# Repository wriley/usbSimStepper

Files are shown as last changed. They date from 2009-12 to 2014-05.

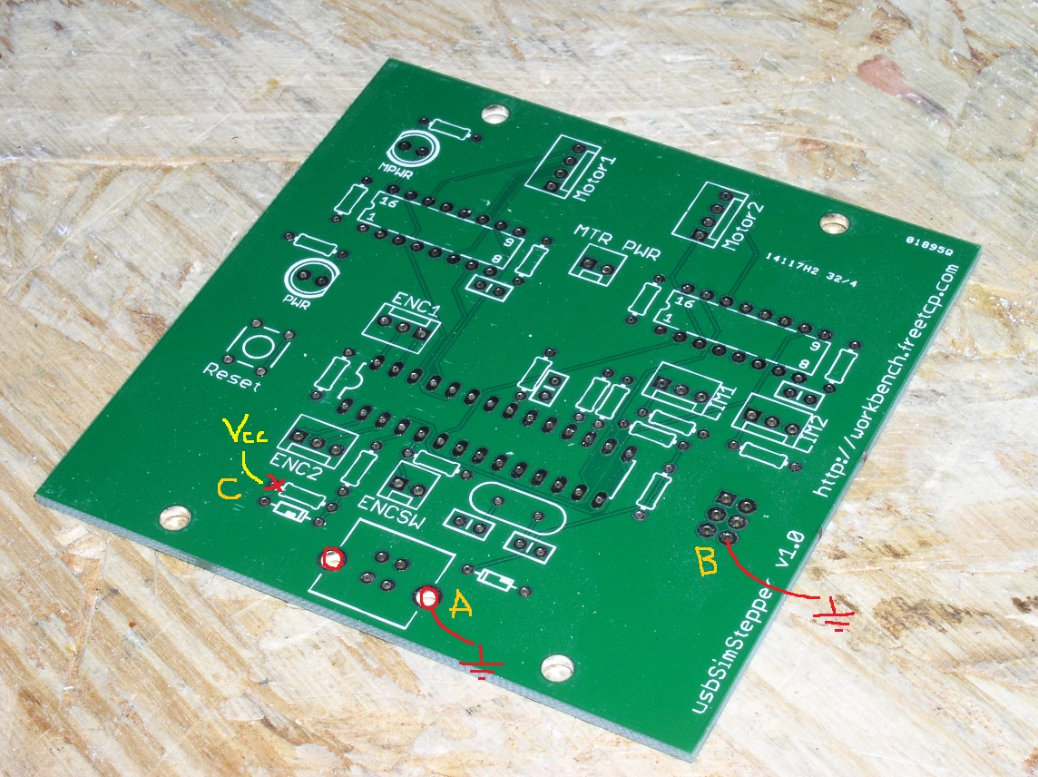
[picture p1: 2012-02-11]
pcb/usbSimStepper v1.0 pcb repair 1.jpg

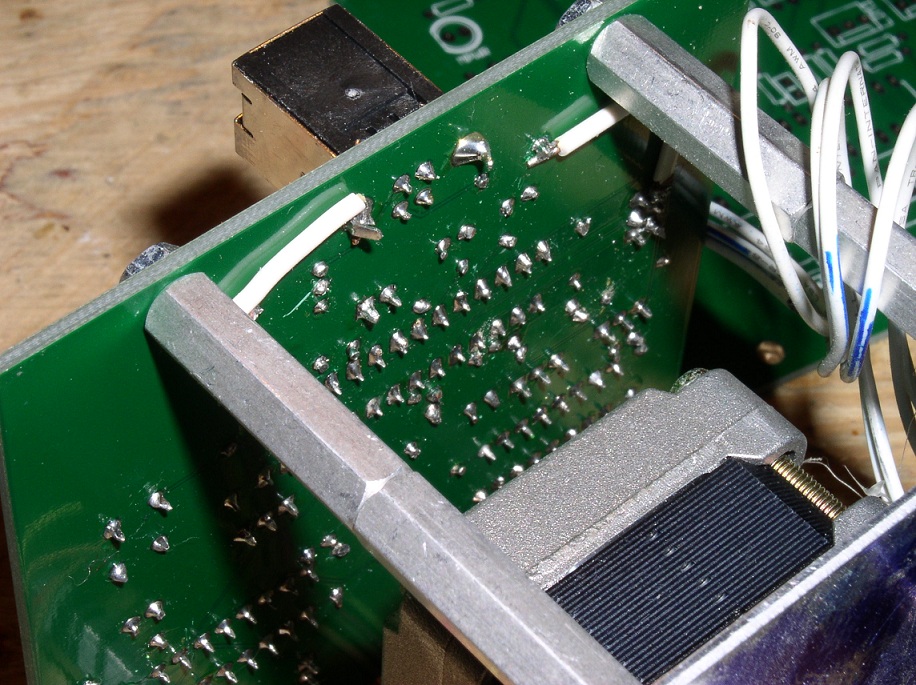
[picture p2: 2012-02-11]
pcb/usbSimStepper v1.0 pcb repair 3.jpg

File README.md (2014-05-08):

usbSimStepper
=============

This is a half-finished project I started several years ago for a flight simulator panel. It is a USB driver board for 1-2 stepper motors built for instruments from Mike Powell's book Building Simulated Aircraft Instrumentation<sup>1</sup>. Windows programs, such as usbSimCentral<sup>2</sup>, can interface with this board via a DLL<sup>3</sup>.

Relevant blog posts
* http://workbench.freetcp.com/archives/549
* http://workbench.freetcp.com/archives/555
* http://workbench.freetcp.com/archives/571
* http://workbench.freetcp.com/archives/739
* http://workbench.freetcp.com/archives/745

References

1. http://www.mikesflightdeck.com/mfdb/bsai/bsai.html
2. https://github.com/wriley/usbSimCentral
3. https://github.com/wriley/usbSimInstrument

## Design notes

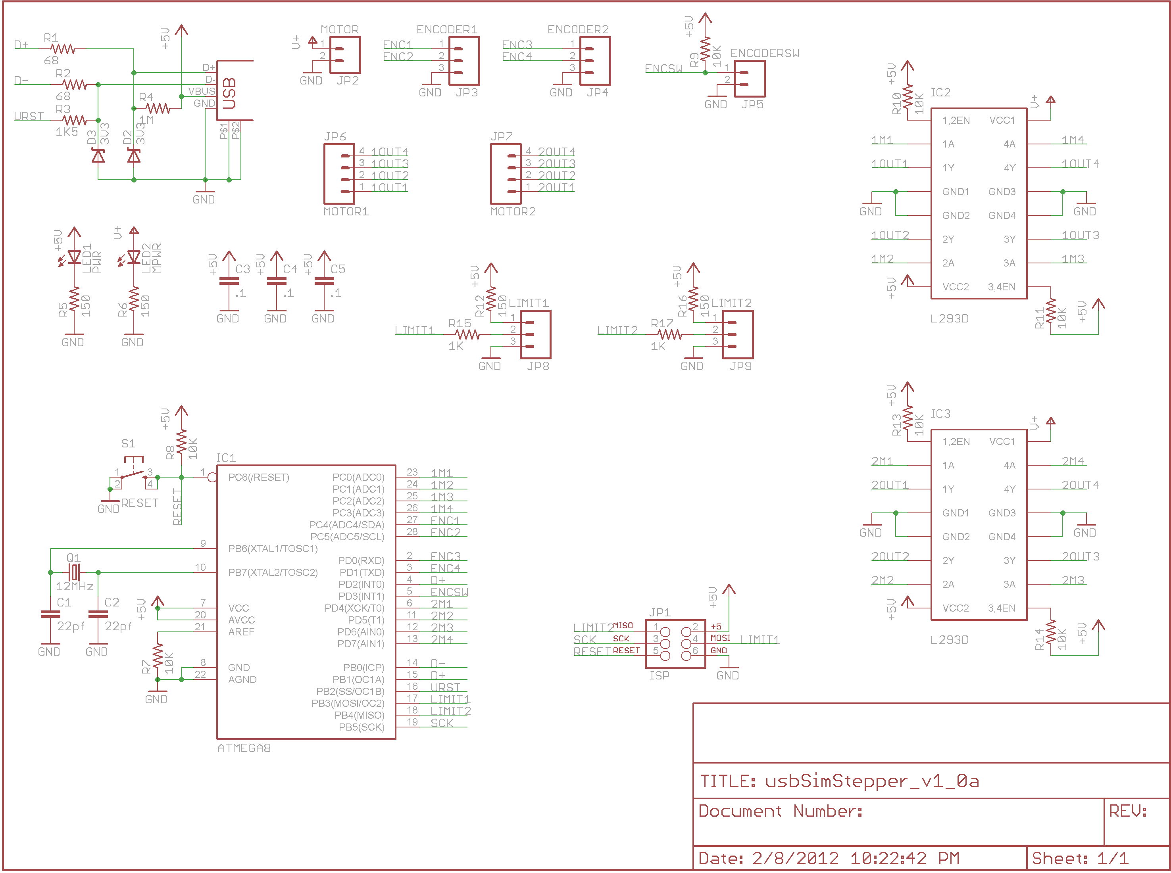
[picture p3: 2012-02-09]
pcb/usbSimStepper_v1_0a_schematic.png

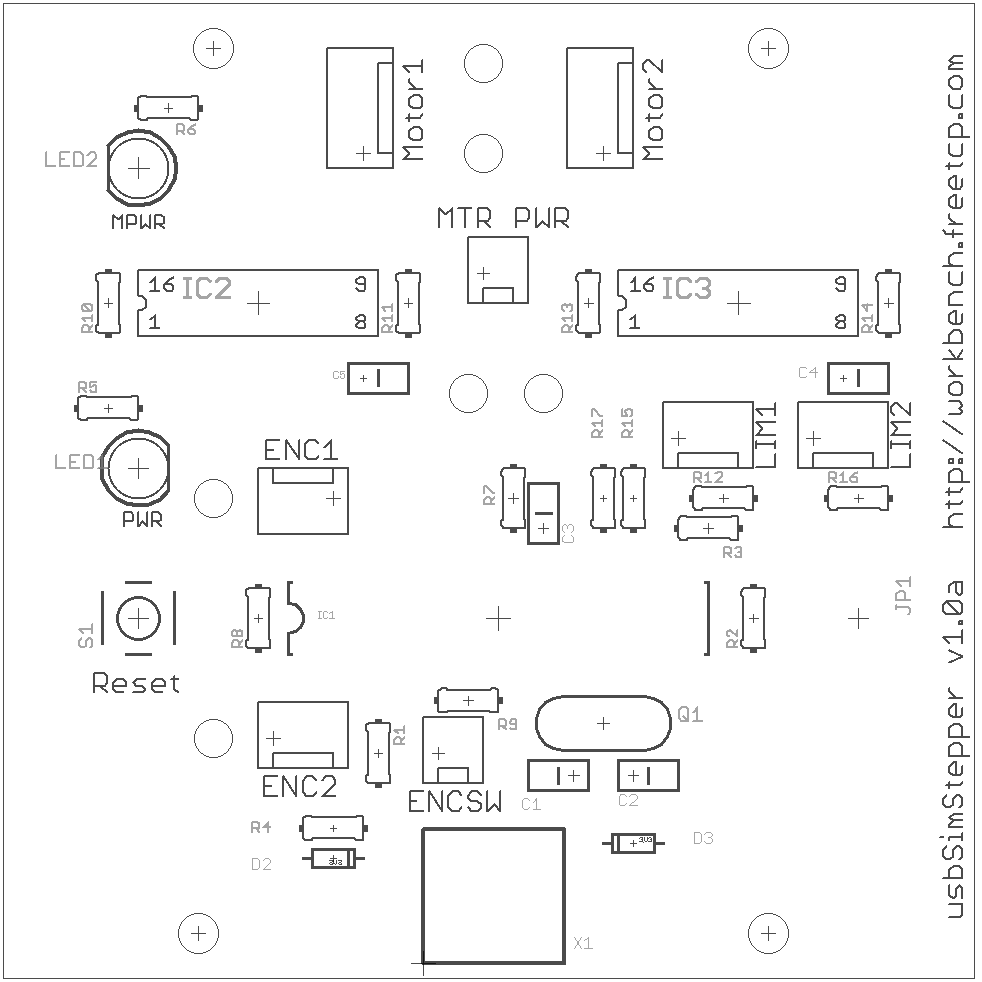
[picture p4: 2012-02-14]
pcb/usbSimStepper_v1_0a_silkscreen.png

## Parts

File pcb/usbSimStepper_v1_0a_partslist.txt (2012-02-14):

Partlist

Exported from usbSimStepper_v1_0a.brd at 2/13/2012 9:21:40 PM

EAGLE Version 6.1.0 Copyright (c) 1988-2012 CadSoft

Assembly variant: 

Part     Value          Package            Library  Position (inch)       Orientation

C1       22pf           CAP-PTH-SMALL2     SparkFun (1.9 0.675)           R180
C2       22pf           CAP-PTH-SMALL2     SparkFun (2.1 0.675)           R0
C3       .1             CAP-PTH-SMALL2     SparkFun (1.8 1.5)             R90
C4       .1             CAP-PTH-SMALL2     SparkFun (2.8 2)               R0
C5       .1             CAP-PTH-SMALL2     SparkFun (1.2 2)               R0
D2       3V3            DIODE-ZENER        SparkFun (1.1 0.4)             R180
D3       3V3            DIODE-ZENER        SparkFun (2.1 0.45)            R0
IC1      ATMEGA8        DIL28-3            SparkFun (1.65 1.2)            R0
IC2      L293D          DIL16              sgs-thom (0.85 2.25)           R0
IC3      L293D          DIL16              sgs-thom (2.45 2.25)           R0
JP1      ISP            2X3-NS             SparkFun (2.85 1.2)            R270
JP2      MOTOR          MOLEX-1X2          SparkFun (1.6 2.35)            R0
JP3      ENCODER1       MOLEX-1X3          SparkFun (1.1 1.6)             R180
JP4      ENCODER2       MOLEX-1X3          SparkFun (0.9 0.8)             R0
JP5      ENCODERSW      MOLEX-1X2          SparkFun (1.45 0.75)           R0
JP6      MOTOR1         MOLEX-1X4          SparkFun (1.2 2.75)            R90
JP7      MOTOR2         MOLEX-1X4          SparkFun (2 2.75)              R90
JP8      LIMIT1         MOLEX-1X3          SparkFun (2.25 1.8)            R0
JP9      LIMIT2         MOLEX-1X3          SparkFun (2.7 1.8)             R0
LED1     PWR            LED5MM             SparkFun (0.45 1.7)            R0
LED2     MPWR           LED5MM             SparkFun (0.45 2.7)            R180
Q1       12MHz          HC49US             SparkFun (2 0.85)              R0
R1       68             0204/7             resistor (1.25 0.75)           R270
R2       68             0204/7             resistor (2.5 1.2)             R90
R3       1K5            0204/7             resistor (2.35 1.5)            R0
R4       1M             0204/7             resistor (1.1 0.5)             R180
R5       150            0204/7             resistor (0.35 1.9)            R0
R6       150            0204/7             resistor (0.55 2.9)            R180
R7       10K            0204/7             resistor (1.7 1.6)             R270
R8       10K            0204/7             resistor (0.85 1.2)            R90
R9       10K            0204/7             resistor (1.55 0.925)          R0
R10      10K            0204/7             resistor (0.35 2.25)           R90
R11      10K            0204/7             resistor (1.35 2.25)           R90
R12      150            0204/7             resistor (2.4 1.6)             R0
R13      10K            0204/7             resistor (1.95 2.25)           R90
R14      10K            0204/7             resistor (2.95 2.25)           R90
R15      1K             0204/7             resistor (2.1 1.6)             R90
R16      150            0204/7             resistor (2.85 1.6)            R0
R17      1K             0204/7             resistor (2 1.6)               R90
S1       RESET          TACTILE-PTH        SparkFun (0.45 1.2)            R90
X1       USB            USB-B-PTH-VERTICAL SparkFun (1.4 0.05)            R0

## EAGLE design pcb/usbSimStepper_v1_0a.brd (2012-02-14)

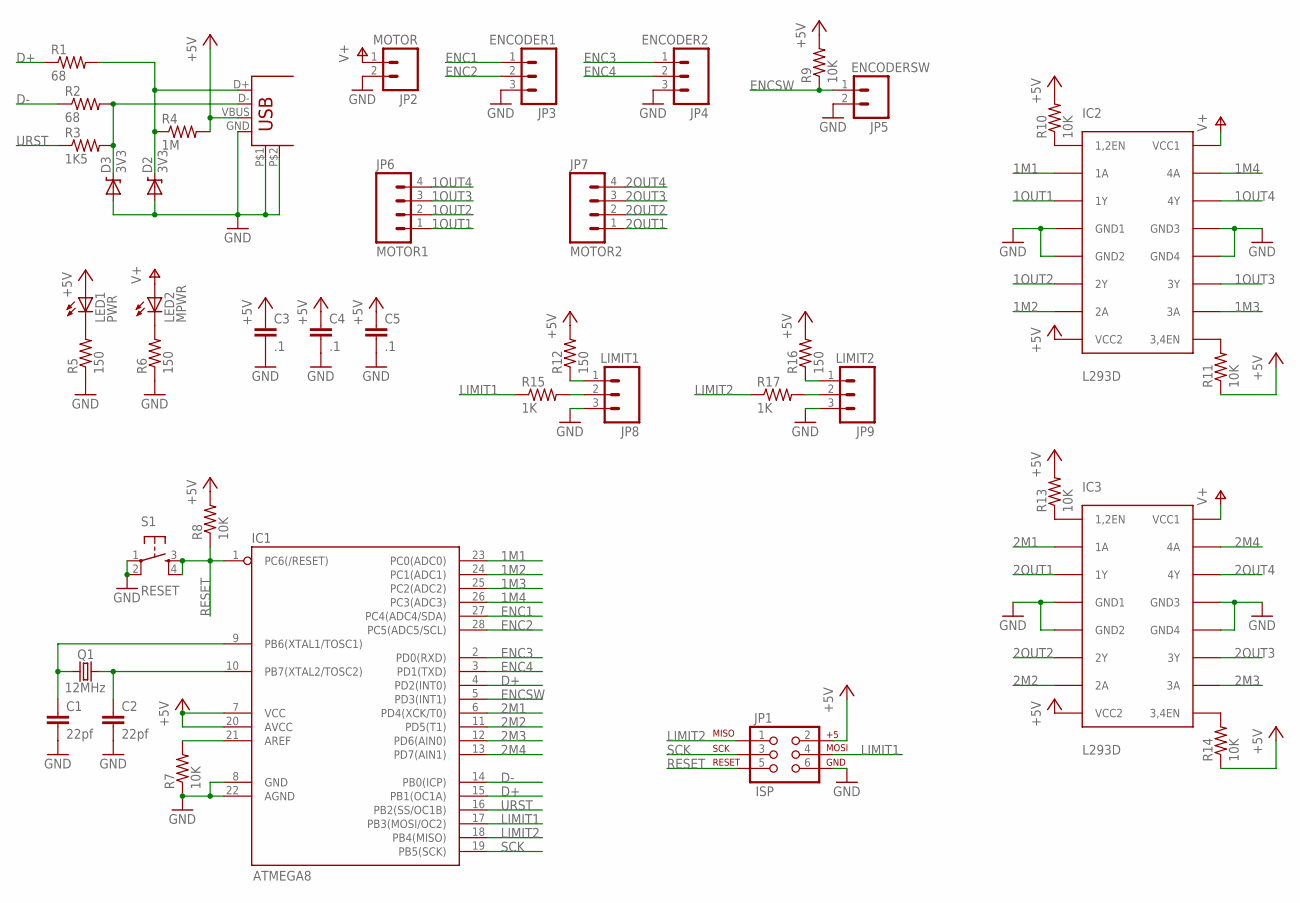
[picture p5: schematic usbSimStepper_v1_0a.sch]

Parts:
C1, C2: 22pf; CAP-PTH-SMALL2
C3, C4, C5: .1; CAP-PTH-SMALL2
D2, D3: 3V3; DIODE-ZENER
IC1: ATMEGA8; DIL28-3
IC2, IC3: L293D; DIL16
JP1: ISP; 2X3-NS
JP2: MOTOR; MOLEX-1X2
JP3: ENCODER1; MOLEX-1X3
JP4: ENCODER2; MOLEX-1X3
JP5: ENCODERSW; MOLEX-1X2
JP6: MOTOR1; MOLEX-1X4
JP7: MOTOR2; MOLEX-1X4
JP8: LIMIT1; MOLEX-1X3
JP9: LIMIT2; MOLEX-1X3
LED1: PWR; LED5MM
LED2: MPWR; LED5MM
Q1: 12MHz; HC49US
R1, R2: 68; 0204/7
R3: 1K5; 0204/7
R4: 1M; 0204/7
R5, R6, R12, R16: 150; 0204/7
R7, R8, R9, R10, R11, R13, R14: 10K; 0204/7
R15, R17: 1K; 0204/7
S1: RESET; TACTILE-PTH
X1: USB; USB-B-PTH-VERTICAL

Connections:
1M1: IC1.23 (PC0(ADC0)), IC2.2 (1A)
1M2: IC1.24 (PC1(ADC1)), IC2.7 (2A)
1M3: IC1.25 (PC2(ADC2)), IC2.10 (3A)
1M4: IC1.26 (PC3(ADC3)), IC2.15 (4A)
1OUT1: IC2.3 (1Y), JP6.1
1OUT2: IC2.6 (2Y), JP6.2
1OUT3: IC2.11 (3Y), JP6.3
1OUT4: IC2.14 (4Y), JP6.4
2M1: IC1.6 (PD4(XCK/T0)), IC3.2 (1A)
2M2: IC1.11 (PD5(T1)), IC3.7 (2A)
2M3: IC1.12 (PD6(AIN0)), IC3.10 (3A)
2M4: IC1.13 (PD7(AIN1)), IC3.15 (4A)
2OUT1: IC3.3 (1Y), JP7.1
2OUT2: IC3.6 (2Y), JP7.2
2OUT3: IC3.11 (3Y), JP7.3
2OUT4: IC3.14 (4Y), JP7.4
+5V: C3.1, C4.1, C5.1, IC1.7 (VCC), IC1.20 (AVCC), IC2.8 (VCC2), IC3.8 (VCC2), JP1.2, LED1.A, R4.2, R8.2, R9.2, R10.2, R11.1, R12.2, R13.2, R14.1, R16.2, X1.VBUS
D+: IC1.4 (PD2(INT0)), IC1.15 (PB1(OC1A)), R1.1
D-: IC1.14 (PB0(ICP)), R2.1
ENC1: IC1.27 (PC4(ADC4/SDA)), JP3.1
ENC2: IC1.28 (PC5(ADC5/SCL)), JP3.2
ENC3: IC1.2 (PD0(RXD)), JP4.1
ENC4: IC1.3 (PD1(TXD)), JP4.2
ENCSW: IC1.5 (PD3(INT1)), JP5.1, R9.1
GND: C1.2, C2.2, C3.2, C4.2, C5.2, D2.P$2 (A), D3.P$2 (A), IC1.8 (GND), IC1.22 (AGND), IC2.4 (GND1), IC2.5 (GND2), IC2.12 (GND4), IC2.13 (GND3), IC3.4 (GND1), IC3.5 (GND2), IC3.12 (GND4), IC3.13 (GND3), JP1.6, JP2.2, JP3.3, JP4.3, JP5.2, JP8.3, JP9.3, R5.1, R6.1, R7.1, S1.1, S1.2, X1.GND, X1.P$1, X1.P$2
LIMIT1: IC1.17 (PB3(MOSI/OC2)), JP1.4, R15.1
LIMIT2: IC1.18 (PB4(MISO)), JP1.1, R17.1
unnamed: D3.P$1 (C), R2.2, R3.2, X1.D-
unnamed: D2.P$1 (C), R1.2, R4.1, X1.D+
unnamed: LED1.K (C), R5.2
unnamed: LED2.K (C), R6.2
unnamed: C1.1, IC1.9 (PB6(XTAL1/TOSC1)), Q1.1
unnamed: C2.1, IC1.10 (PB7(XTAL2/TOSC2)), Q1.2
unnamed: IC1.21 (AREF), R7.2
unnamed: JP8.1, R12.1
unnamed: JP8.2, R15.2
unnamed: JP9.1, R16.1
unnamed: IC3.1 (1,2EN), R13.1
unnamed: IC3.9 (3,4EN), R14.2
unnamed: IC2.1 (1,2EN), R10.1
unnamed: IC2.9 (3,4EN), R11.2
unnamed: JP9.2, R17.2
RESET: IC1.1 (PC6(/RESET)), JP1.5, R8.1, S1.3, S1.4
SCK: IC1.19 (PB5(SCK)), JP1.3
URST: IC1.16 (PB2(SS/OC1B)), R3.1
V+: IC2.16 (VCC1), IC3.16 (VCC1), JP2.1, LED2.A

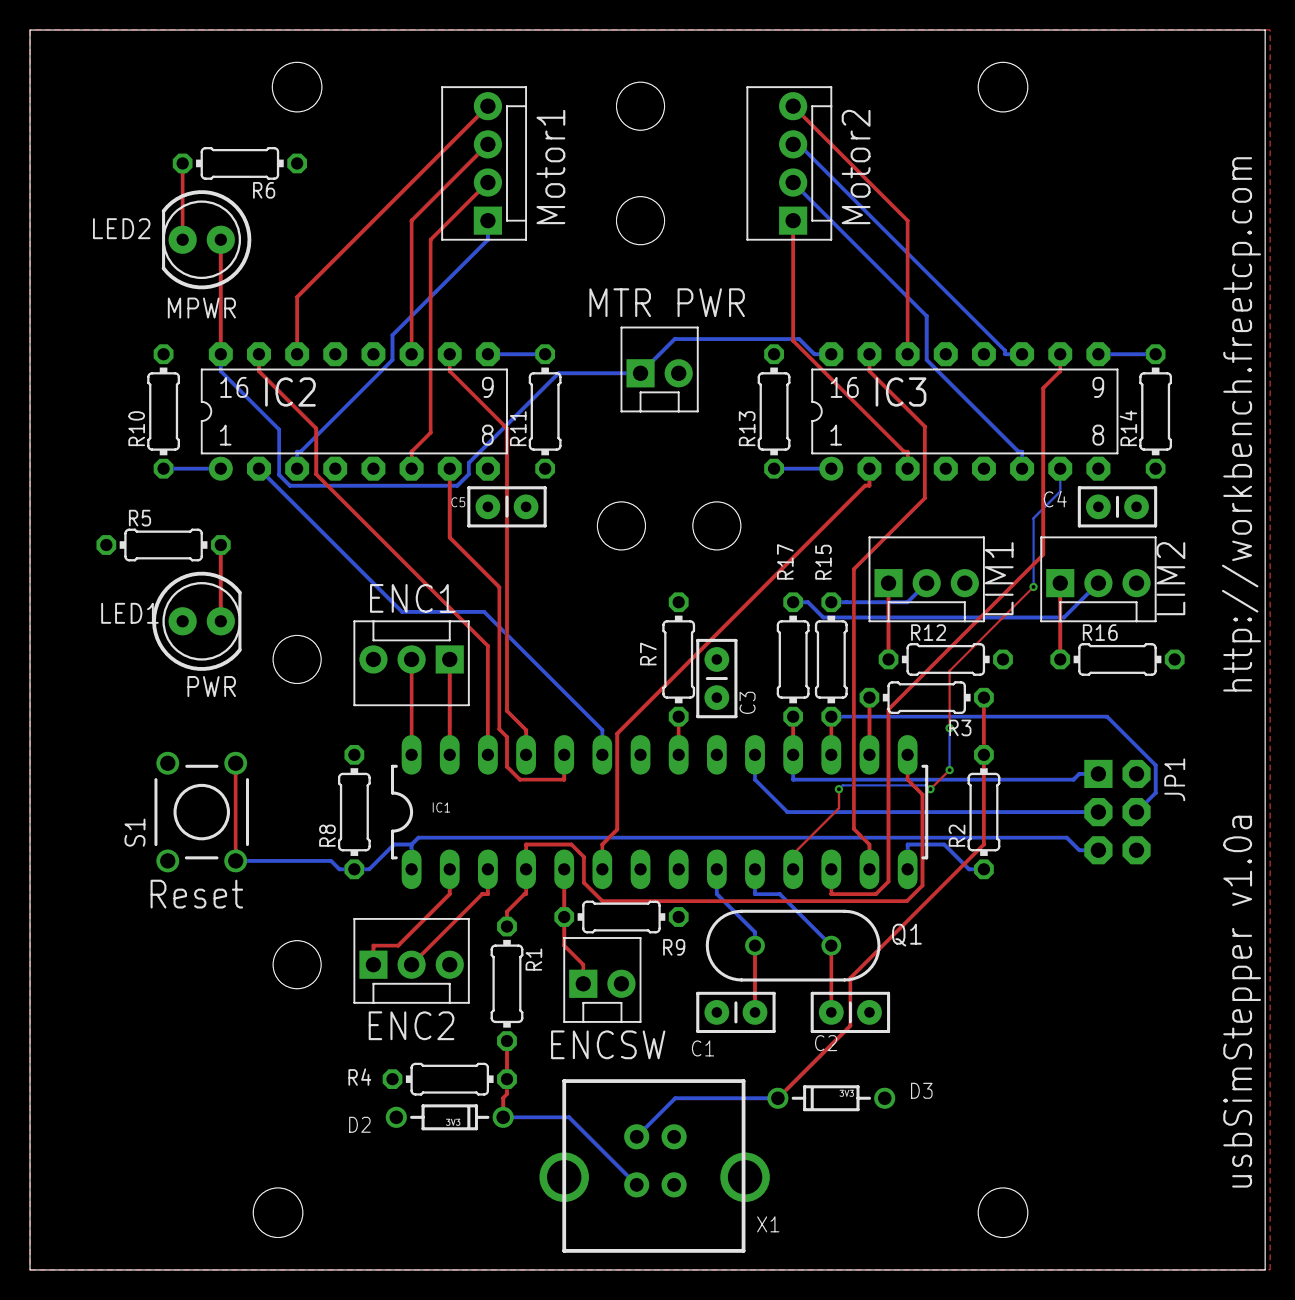
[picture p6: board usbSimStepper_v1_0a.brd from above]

Board: 2 copper layers, 82.2 x 82.5 mm, 45 parts (0 on the bottom side), 46 nets.

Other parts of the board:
U$1, U$2, U$3, U$4: STAND-OFF

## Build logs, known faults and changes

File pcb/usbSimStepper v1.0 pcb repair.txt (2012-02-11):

usbSimStepper v1.0 PCB error repair notes

Reference image "usbSimStepper v1.0 pcb repair 1.jpg" for steps A, B, and C.
A) The USB connector shields are not tied to GND (bottom plane).
   Connect either shield connection to any convenient GND location

B) The GND pin on the ISP connector (2x3-pin header) is not tied to GND (bottom plane).
   Connect pin 6 to any convenient GND location

C) Resistor R4 is tied to GND (bottom plane) instead of Vcc (top plane).
   Do not solder the end of R4 marked with red X, instead connect that end to any
   convenient Vcc location.

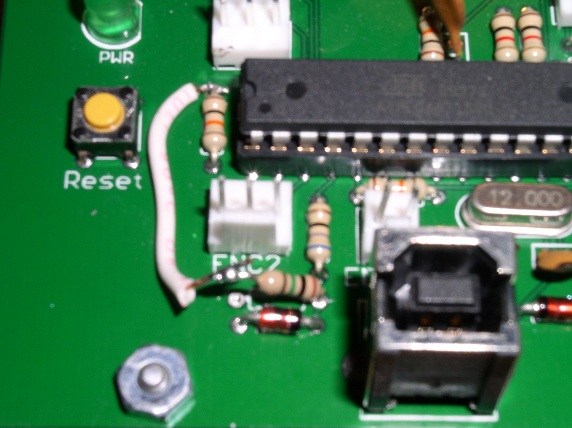
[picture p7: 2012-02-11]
pcb/usbSimStepper v1.0 pcb repair 2.jpg

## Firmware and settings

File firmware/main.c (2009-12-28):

#include <stdlib.h>
#include <avr/io.h>
#include <avr/interrupt.h>
#include <avr/pgmspace.h>
#include <avr/eeprom.h>
#include <avr/wdt.h>

#include "usbdrv.h"
#include "oddebug.h"
#include <util/delay.h>

// Uncomment if instrument is meant to go in continuous circles, such as a gyrocompass
// Comment out for instruments such as ASI
//#define FULLCIRCLE

// Uncomment to support second stepper motor, opto and encoder
//#define MOTOR2

#define ENCODER1PORT            PORTD
#define ENCODER1DDR             DDRD
#define ENCODER1PIN             PIND
#define PHASE_A_1               (ENCODER1PIN & 1<<1)
#define PHASE_B_1               (ENCODER1PIN & 1<<0)
#define OPTO1PORT               PORTB
#define OPTO1DDR                DDRB
#define OPTO1PIN                PINB
#define OPTO1                   (OPTO1PIN & 1<<3)
#define MOTOR1PORT              PORTC
#define MOTOR1DDR               DDRC
#define MOTOR1MASK				0x0f

#define CMD_ECHO				0
#define CMD_SET1				1
#define CMD_SET2				2
#define CMD_GET_TABLE			10
#define CMD_SET_TABLE			11
#define CMD_GET_TABLERAW		20
#define CMD_SET_TABLERAW		21
#ifdef MOTOR2
#define CMD_GET_TABLE2			30
#define CMD_SET_TABLE2			31
#define CMD_GET_TABLERAW2		40
#define CMD_SET_TABLERAW2		41
#endif
#define CMD_RESET				99

#ifdef MOTOR2
#define ENCODER2PORT            PORTD
#define ENCODER2DDR             DDRD
#define ENCODER2PIN             PIND
#define PHASE_A_2               (ENCODER2PIN & 1<<1)
#define PHASE_B_2               (ENCODER2PIN & 1<<0)
#define OPTO2PORT               PORTB
#define OPTO2DDR                DDRB
#define OPTO2PIN                PINB
#define OPTO2                   (OPTO2PIN & 1<<3)
#define MOTOR2PORT              PORTC
#define MOTOR2DDR               DDRC
#define MOTOR2MASK				0x0f
#endif

#define FORWARD                 0
#define REVERSE                 1
#define HALFWAY					199
#define MAXPOS					399
#define EEPROM_SERIAL_LOCATION	0

#define EEPROM_TABLE_LOCATION		8
#define EEPROM_TABLERAW_LOCATION	72
#ifdef MOTOR2
#define EEPROM_TABLE2_LOCATION		136
#define EEPROM_TABLERAW2_LOCATION	200
#endif

// positions for half stepping bipolar
static char motorPositions[8] = {
    0x09,   // 0 0 0 0  1 0 0 1
    0x01,   // 0 0 0 0  0 0 0 1
    0x05,   // 0 0 0 0  0 1 0 1
    0x04,   // 0 0 0 0  0 1 0 0
    0x06,   // 0 0 0 0  0 1 1 0
    0x02,   // 0 0 0 0  0 0 1 0
    0x0a,   // 0 0 0 0  1 0 1 0
    0x08    // 0 0 0 0  1 0 0 0
};

static int16_t last1;
static int16_t position1 = 0;
static int16_t newposition1 = 0;
static int8_t mtr_direction1 = REVERSE;
static int16_t stepCounter1 = 0;
static int16_t mtr_delta1 = 0x0000;
static int8_t goHome1 = 0x02;
static int16_t testCount1 = 0;

#ifdef MOTOR2
static int16_t last2;
static int16_t position2 = 0;
static int16_t newposition2 = 0;
static int8_t mtr_direction2 = REVERSE;
static int16_t stepCounter2 = 0;
static int16_t mtr_delta2 = 0x0000;
static int8_t goHome2 = 0x02;
static int16_t testCount2 = 0;
#endif

#define SERIAL_NUMBER_LENGTH 1
static int  serialNumberDescriptor[SERIAL_NUMBER_LENGTH + 1];

static void SetSerial(void)
{
   serialNumberDescriptor[0] = USB_STRING_DESCRIPTOR_HEADER(SERIAL_NUMBER_LENGTH);
   serialNumberDescriptor[1] = eeprom_read_byte(EEPROM_SERIAL_LOCATION);
}

USB_PUBLIC uchar usbFunctionSetup(uchar data[8])
{
usbRequest_t    *rq = (void *)data;
static uchar    replyBuf[8];

    usbMsgPtr = replyBuf;
    if(rq->bRequest == CMD_ECHO){
        replyBuf[0] = rq->wValue.bytes[0];
        replyBuf[1] = rq->wValue.bytes[1];
        return 2;
    } else if(rq->bRequest == CMD_SET1){
		newposition1 = 0x0000;
		newposition1 <<= 8;
        newposition1 |= rq->wValue.bytes[1];
		newposition1 <<= 8;
        newposition1 |= rq->wValue.bytes[0];
#ifdef MOTOR2
	} else if(rq->bRequest == CMD_SET2){
		newposition2 = 0x0000;
		newposition2 <<= 8;
        newposition2 |= rq->wValue.bytes[1];
		newposition2 <<= 8;
        newposition2 |= rq->wValue.bytes[0];
#endif
    } else if(rq->bRequest == CMD_GET_TABLE){
		for(uchar i = 0; i < 8; i++){
			replyBuf[i] = eeprom_read_byte(EEPROM_TABLE_LOCATION + (rq->wValue.bytes[0] * 8) + i);
		}
		return 8;
    } else if(rq->bRequest == CMD_SET_TABLE){
		eeprom_write_byte(EEPROM_TABLE_LOCATION + (rq->wValue.bytes[0] * 8) + (rq->wValue.bytes[1]), rq->wIndex.bytes[0]);
	} else if(rq->bRequest == CMD_GET_TABLERAW){
		for(uchar i = 0; i < 8; i++){
			replyBuf[i] = eeprom_read_byte(EEPROM_TABLERAW_LOCATION + (rq->wValue.bytes[0] * 8) + i);
		}
		return 8;
    } else if(rq->bRequest == CMD_SET_TABLERAW){
		eeprom_write_byte(EEPROM_TABLERAW_LOCATION + (rq->wValue.bytes[0] * 8) + (rq->wValue.bytes[1]), rq->wIndex.bytes[0]);
#ifdef MOTOR2
    } else if(rq->bRequest == CMD_GET_TABLE2){
		for(uchar i = 0; i < 8; i++){
			replyBuf[i] = eeprom_read_byte(EEPROM_TABLE2_LOCATION + (rq->wValue.bytes[0] * 8) + i);
		}
		return 8;
    } else if(rq->bRequest == CMD_SET_TABLE2){
		eeprom_write_byte(EEPROM_TABLE2_LOCATION + (rq->wValue.bytes[0] * 8) + (rq->wValue.bytes[1]), rq->wIndex.bytes[0]);
	} else if(rq->bRequest == CMD_GET_TABLERAW2){
		for(uchar i = 0; i < 8; i++){
			replyBuf[i] = eeprom_read_byte(EEPROM_TABLERAW2_LOCATION + (rq->wValue.bytes[0] * 8) + i);
		}
		return 8;
    } else if(rq->bRequest == CMD_SET_TABLERAW2){
		eeprom_write_byte(EEPROM_TABLERAW2_LOCATION + (rq->wValue.bytes[0] * 8) + (rq->wValue.bytes[1]), rq->wIndex.bytes[0]);
#endif
	} else if(rq->bRequest == CMD_RESET){
		newposition1 = 0;
		position1 = 0;
		goHome1 = 2;
    }
    return 0;
}

uchar usbFunctionDescriptor(usbRequest_t *rq)
{
   uchar len = 0;
   usbMsgPtr = 0;
   if (rq->wValue.bytes[1] == USBDESCR_STRING && rq->wValue.bytes[0] == 3)
   {
      usbMsgPtr = (uchar*)serialNumberDescriptor;
      len = sizeof(serialNumberDescriptor);
   }
   return len;
}

SIGNAL (SIG_OUTPUT_COMPARE2)                // 1ms
{
    int16_t new1, diff1;

    new1 = 0;
    if( PHASE_A_1 )
        new1 = 3;
    if( PHASE_B_1 )
        new1 ^= 1;                          // convert gray to binary
    diff1 = last1 - new1;                   // difference last - new
    if( diff1 & 1 ){                        // bit 0 = value (1)
        last1 = new1;                       // store new as next last
		position1 += (diff1 & 2) - 1;		// update position1
    }

#ifdef MOTOR2
	int16_t new2, diff2;

    new2 = 0;
    if( PHASE_A_2 )
        new2 = 3;
    if( PHASE_B_2 )
        new2 ^= 1;                          // convert gray to binary
    diff2 = last2 - new2;                   // difference last - new
    if( diff2 & 1 ){                        // bit 0 = value (1)
        last2 = new2;                       // store new as next last
		position2 += (diff2 & 2) - 1;		// update position1
    }
#endif

    if(goHome1 > 0)
    {
		if(goHome1 == 3) // test mode
		{
			if(testCount1 < MAXPOS)
			{
				testCount1++;
				stepCounter1++;
				stepCounter1 &= 0x07;
            	MOTOR1PORT = motorPositions[stepCounter1] & MOTOR1MASK;
			}
			else
			{
				goHome1 = 4;
			}
		}

        if(goHome1 == 2) // move forward until opto is not dark
        {
            if(OPTO1PIN & OPTO1) // dark
            {
                stepCounter1++;
				stepCounter1 &= 0x07;
                MOTOR1PORT = motorPositions[stepCounter1] & MOTOR1MASK;
            }
            else
            {
                goHome1 = 1;
            }
        }
        
        if(goHome1 == 1) // move backward until opto is dark
        {
            if(OPTO1PIN & OPTO1) // dark
            {
                goHome1 = 0;
            }
            else
            {
                stepCounter1--;
				stepCounter1 &= 0x07;
                MOTOR1PORT = motorPositions[stepCounter1] & MOTOR1MASK;
            }
        }
    }
    else
    {
		if(newposition1 > MAXPOS) { newposition1 = MAXPOS; }
		if(newposition1 < 0) { newposition1 = 0; }
        mtr_delta1 = newposition1 - position1;
        if(mtr_delta1 != 0)
        {
            if(mtr_delta1 < 0)
            {
                mtr_direction1 = REVERSE;
            }
            else
            {
                mtr_direction1 = FORWARD;
            }

#ifdef FULLCIRCLE
            if(abs(mtr_delta1) > HALFWAY)
            {
                if(mtr_direction1 == FORWARD)
                {
                    mtr_direction1 = REVERSE;
                } else if(mtr_direction1 == REVERSE)
				{
					mtr_direction1 = FORWARD;
				}
            }
#endif

            if(mtr_direction1 == REVERSE)
            {
                position1--;
#ifdef FULLCIRCLE
				if(position1 < 0){ position1 = MAXPOS; }
#else
				if(position1 < 0){ position1 = 0; }
#endif
                stepCounter1--;
            }
            else
            {
                position1++;
#ifdef FULLCIRCLE
                if(position1 > MAXPOS){ position1 = 0; }
#else
				if(position1 > MAXPOS){ position1 = MAXPOS; }
#endif
				stepCounter1++;
            }
            
			stepCounter1 &= 0x07;
            MOTOR1PORT = motorPositions[stepCounter1] & MOTOR1MASK;
        }
    }

#ifdef MOTOR2
    if(goHome2 > 0)
    {
		if(goHome2 == 3) // test mode
		{
			if(testCount2 < MAXPOS)
			{
				testCount2++;
				stepCounter2++;
				stepCounter2 &= 0x07;
            	MOTOR2PORT = motorPositions[stepCounter2] & MOTOR2MASK;
			}
			else
			{
				goHome2 = 4;
			}
		}

        if(goHome2 == 2) // move forward until opto is not dark
        {
            if(OPTO2PIN & OPTO2) // dark
            {
                stepCounter2++;
				stepCounter2 &= 0x07;
                MOTOR2PORT = motorPositions[stepCounter2] & MOTOR2MASK;
            }
            else
            {
                goHome2 = 1;
            }
        }
        
        if(goHome2 == 1) // move backward until opto is dark
        {
            if(OPTO2PIN & OPTO2) // dark
            {
                goHome2 = 0;
            }
            else
            {
                stepCounter2--;
				stepCounter2 &= 0x07;
                MOTOR2PORT = motorPositions[stepCounter2] & MOTOR2MASK;
            }
        }
    }
    else
    {
		if(newposition2 > MAXPOS) { newposition2 = MAXPOS; }
		if(newposition2 < 0) { newposition2 = 0; }
        mtr_delta2 = newposition2 - position2;
        if(mtr_delta2 != 0)
        {
            if(mtr_delta2 < 0)
            {
                mtr_direction2 = REVERSE;
            }
            else
            {
                mtr_direction2 = FORWARD;
            }

#ifdef FULLCIRCLE
            if(abs(mtr_delta2) > HALFWAY)
            {
                if(mtr_direction2 == FORWARD)
                {
                    mtr_direction2 = REVERSE;
                } else if(mtr_direction2 == REVERSE)
				{
					mtr_direction2 = FORWARD;
				}
            }
#endif

            if(mtr_direction2 == REVERSE)
            {
                position2--;
#ifdef FULLCIRCLE
				if(position2 < 0){ position2 = MAXPOS; }
#else
				if(position2 < 0){ position2 = 0; }
#endif
                stepCounter2--;
            }
            else
            {
                position2++;
#ifdef FULLCIRCLE
                if(position2 > MAXPOS){ position2 = 0; }
#else
				if(position2 > MAXPOS){ position2 = MAXPOS; }
#endif
				stepCounter2++;
            }
            
			stepCounter2 &= 0x07;
            MOTOR2PORT = motorPositions[stepCounter2] & MOTOR2MASK;
        }
    }
#endif
}

int main(void)
{
	uchar   i;

	SetSerial();

    wdt_enable(WDTO_1S);
    odDebugInit();
    DDRD = ~(1 << 2);   /* all outputs except PD2 = INT0 */
    PORTD = 0;
    PORTB = 0;          /* no pullups on USB pins */
/* We fake an USB disconnect by pulling D+ and D- to 0 during reset. This is
 * necessary if we had a watchdog reset or brownout reset to notify the host
 * that it should re-enumerate the device. Otherwise the host's and device's
 * concept of the device-ID would be out of sync.
 */
    DDRB = ~USBMASK;    /* set all pins as outputs except USB */
    usbDeviceDisconnect();  /* enforce re-enumeration, do this while interrupts are disabled! */
    i = 0;
    while(--i){         /* fake USB disconnect for > 500 ms */
        wdt_reset();
        _delay_ms(2);
    }
    usbDeviceConnect();
    TCCR0 = 5;          /* set prescaler to 1/1024 */
    usbInit();

	DDRB &= ~(_BV(PB3));
	PORTB |= _BV(PB3);
	
	DDRD &= ~(_BV(PD0)|_BV(PD1));
	PORTD |= (_BV(PD0)|_BV(PD1));

	TCNT2 = 0x00; /* Timer 2: Reset counter (periodic timer) */
	TCCR2 = 0x0f; /* Clock / 1024, clear after compare match (CTC) */
	OCR2 = 0x0b;

	TIMSK |= _BV(OCIE2);

	DDRC = 0x2f;
	PORTC = 0x2f;

    sei();
    for(;;){    /* main event loop */
        wdt_reset();
        usbPoll();
    }
    return 0;
}

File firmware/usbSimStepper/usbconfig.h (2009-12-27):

/* Name: usbconfig.h
 * Project: AVR USB driver
 * Author: Christian Starkjohann
 * Creation Date: 2005-04-01
 * Tabsize: 4
 * Copyright: (c) 2005 by OBJECTIVE DEVELOPMENT Software GmbH
 * License: GNU GPL v2 (see License.txt) or proprietary (CommercialLicense.txt)
 * This Revision: $Id: usbconfig.h 43 2005-04-10 21:04:36Z cs $
 */

#ifndef __usbconfig_h_included__
#define __usbconfig_h_included__

/*
General Description:
This file contains parts of the USB driver which can be configured and can or
must be adapted to your hardware.

Please note that the usbdrv contains a usbconfig-prototype.h file now. We
recommend that you use that file as a template because it will always list
the newest features and options.
*/

/* ---------------------------- Hardware Config ---------------------------- */

#define USB_CFG_IOPORTNAME      B
/* This is the port where the USB bus is connected. When you configure it to
 * "B", the registers PORTB, PINB and DDRB will be used.
 */
#define USB_CFG_DMINUS_BIT      0
/* This is the bit number in USB_CFG_IOPORT where the USB D- line is connected.
 * This may be any bit in the port.
 */
#define USB_CFG_DPLUS_BIT       1
/* This is the bit number in USB_CFG_IOPORT where the USB D+ line is connected.
 * This may be any bit in the port. Please note that D+ must also be connected
 * to interrupt pin INT0!
 */
/* #define USB_CFG_CLOCK_KHZ       (F_CPU/1000) */
/* Clock rate of the AVR in MHz. Legal values are 12000, 16000 or 16500.
 * The 16.5 MHz version of the code requires no crystal, it tolerates +/- 1%
 * deviation from the nominal frequency. All other rates require a precision
 * of 2000 ppm and thus a crystal!
 * Default if not specified: 12 MHz
 */

/* ----------------------- Optional Hardware Config ------------------------ */

#define USB_CFG_PULLUP_IOPORTNAME   B
/* If you connect the 1.5k pullup resistor from D- to a port pin instead of
 * V+, you can connect and disconnect the device from firmware by calling
 * the macros usbDeviceConnect() and usbDeviceDisconnect() (see usbdrv.h).
 * This constant defines the port on which the pullup resistor is connected.
 */
#define USB_CFG_PULLUP_BIT          2
/* This constant defines the bit number in USB_CFG_PULLUP_IOPORT (defined
 * above) where the 1.5k pullup resistor is connected. See description
 * above for details.
 */

/* --------------------------- Functional Range ---------------------------- */

#define USB_CFG_HAVE_INTRIN_ENDPOINT    0
/* Define this to 1 if you want to compile a version with two endpoints: The
 * default control endpoint 0 and an interrupt-in endpoint 1.
 */
#define USB_CFG_HAVE_INTRIN_ENDPOINT3   0
/* Define this to 1 if you want to compile a version with three endpoints: The
 * default control endpoint 0, an interrupt-in endpoint 1 and an interrupt-in
 * endpoint 3. You must also enable endpoint 1 above.
 */
#define USB_CFG_IMPLEMENT_HALT          0
/* Define this to 1 if you also want to implement the ENDPOINT_HALT feature
 * for endpoint 1 (interrupt endpoint). Although you may not need this feature,
 * it is required by the standard. We have made it a config option because it
 * bloats the code considerably.
 */
#define USB_CFG_INTR_POLL_INTERVAL      10
/* If you compile a version with endpoint 1 (interrupt-in), this is the poll
 * interval. The value is in milliseconds and must not be less than 10 ms for
 * low speed devices.
 */
#define USB_CFG_IS_SELF_POWERED         0
/* Define this to 1 if the device has its own power supply. Set it to 0 if the
 * device is powered from the USB bus.
 */
#define USB_CFG_MAX_BUS_POWER           20
/* Set this variable to the maximum USB bus power consumption of your device.
 * The value is in milliamperes. [It will be divided by two since USB
 * communicates power requirements in units of 2 mA.]
 */
#define USB_CFG_IMPLEMENT_FN_WRITE      0
/* Set this to 1 if you want usbFunctionWrite() to be called for control-out
 * transfers. Set it to 0 if you don't need it and want to save a couple of
 * bytes.
 */
#define USB_CFG_IMPLEMENT_FN_READ       0
/* Set this to 1 if you need to send control replies which are generated
 * "on the fly" when usbFunctionRead() is called. If you only want to send
 * data from a static buffer, set it to 0 and return the data from
 * usbFunctionSetup(). This saves a couple of bytes.
 */
#define USB_CFG_IMPLEMENT_FN_WRITEOUT   0
/* Define this to 1 if you want to use interrupt-out (or bulk out) endpoint 1.
 * You must implement the function usbFunctionWriteOut() which receives all
 * interrupt/bulk data sent to endpoint 1.
 */
#define USB_CFG_HAVE_FLOWCONTROL        0
/* Define this to 1 if you want flowcontrol over USB data. See the definition
 * of the macros usbDisableAllRequests() and usbEnableAllRequests() in
 * usbdrv.h.
 */
/* #define USB_RX_USER_HOOK(data, len)     if(usbRxToken == (uchar)USBPID_SETUP) blinkLED(); */
/* This macro is a hook if you want to do unconventional things. If it is
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

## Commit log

2009-02-03 usbSimStepper-v10.sch: added eagle schematic
    [usbSimStepper-v10.sch]
2009-02-04 finished schematic and created board
    [usbSimStepper-v10.brd, usbSimStepper-v10.sch]
2009-02-04 usbSimStepper-v10.brd: checking in unrouted version usbSimStepper-v10-routed.brd: separate file for routed version
    [usbSimStepper-v10-routed.brd, usbSimStepper-v10.brd]
2009-02-04 added filter cap for stepper chip
    [usbSimStepper-v10-routed.brd, usbSimStepper-v10.brd, usbSimStepper-v10.sch]
2009-02-05 first attempt at supporting dual stepper motors
    [usbSimStepper-v10.brd, usbSimStepper-v10.sch]
2009-02-09 added optical interrupter connections
    [usbSimStepper-v10.brd, usbSimStepper-v10.sch]
2009-06-01 added ExpressPCB schematic and PCB files
    [usbSimStepper.sch]
2009-07-02 change motor power connector
    [usbSimStepper.sch]
2009-09-23 created directory structure deleted old eagle and ExpressPCB directories
    [usbSimStepper-v10-routed.brd, usbSimStepper-v10.brd, usbSimStepper-v10.sch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]
2009-09-23 added l293's
    [usbSimStepper.sch]
2009-09-24 usbSimStepper.sch: finished schematic usbSimStepper.brd: blank board with standoff holes
    [usbSimStepper.brd, usbSimStepper.sch]
2009-09-24 usbSimStepper.brd: first attempt at component placement
    [usbSimStepper.brd]
2009-09-24 added filter cap for power
    [usbSimStepper.brd, usbSimStepper.sch]
2009-09-24 ERC fixes
    [usbSimStepper.brd, usbSimStepper.sch]
2009-09-24 some clean up of name/value placement added power and ground planes
    [usbSimStepper.brd, usbSimStepper.sch]
2009-09-24 board updates and added limit sensor connections
    [usbSimStepper.brd, usbSimStepper.sch]
2009-09-24 renaming for v1.0
    [usbSimStepper_v1_0.brd, usbSimStepper_v1_0.sch]
2009-09-24 added freerouting.net files added zip of gerber files
    [usbSimStepper_v1_0.dsn]
2009-09-24 added POV files for Eagle3D
    [usbSimStepper_v1_0.brd]
2009-09-24 added firmware: this is untested and is ported from a prototype single stepper breadboard setup
2009-09-24 usbSimStepper_v1_0_schematic.png: added schematic image
2009-09-25 Fixed one typo, compiles now but still untested
    [main.c]
2009-12-26 dual motor version tested with single motor
2012-02-09 version 1.0a fixes these board errors 1) No GND on ISP 2) No GND to USB shield 3) usb 1M resistor tied to GND instead of Vcc
    [usbSimStepper_v1_0.brd, usbSimStepper_v1_0.dsn, usbSimStepper_v1_0.sch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]
2012-02-10 Added driver
2012-02-11 added notes for repair of PCB v1.0
2012-02-14 pcb: silkscreen updates
    [usbSimStepper_v1_0a.brd]

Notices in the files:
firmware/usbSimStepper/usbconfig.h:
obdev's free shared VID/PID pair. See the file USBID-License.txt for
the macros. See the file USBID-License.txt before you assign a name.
